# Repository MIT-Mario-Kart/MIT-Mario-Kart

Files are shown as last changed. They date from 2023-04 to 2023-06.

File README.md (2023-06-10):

# MIT - Mario Kart

## Intro
In this project, we planned on creating our own adapted version of Mario Kart in real life. 
The goal was to create a circuit on which we would have 6 small remote-controlled cars, each car controlled either by an AI or by a player. 
We had imagined a few powerups that cars could collect, that would either affect the car collecting it or the other cars. 
There are three main parts to this project: an overhead camera that extracts simple shapes and colours from an image in order to be able to track each car’s position, 
the track and cars themselves, and lastly the main server controlling each individual car.  
You can find our initial project proposal [here](MIT_Team_Proposal.pdf).

## Summary 

- [Cars](#cars)

  - [Electrical Components](#electrical-components)

  - [Connections and circuitry](#connections-and-circuitry)

  - [Color sensor calibration](#color-sensor-calibration)

  - [3D-design](#3d-design)

- [Circuit Design](#circuit-design)

- [Phone Holder](#phone-holder)

  - [MDF structure](#mdf-structure)

  - [3D printed holder](#3d-printed-holder)

- [iOS Application for Cars Detection](#ios-application-for-cars-detection)

  - [Reliable Coordinate System](#reliable-coordinate-system)

  - [Calibrating the circuit](#calibrating-the-circuit)

  - [Detecting cars and their orientation](#detecting-cars-and-their-orientation)

  - [Performance](#performance)

  - [Potential Drawback](#potential-drawback)

- [AI Algorithm](#ai-algorithm)

  - [Overview](#overview)

    - [Flowmap](#flowmap)

    - [Acceleration](#acceleration)

    - [Powerups](#powerups)

    - [Overtake](#overtake)

  - [AI Simulation](#ai-simulation)

- [Server](#server)

  - [Overview](#overview-1)

  - [Camera connection](#camera-connection)

    - [ID system](#id-system)

    - [Updating the cars based on the information from the camera](#updating-the-cars-based-on-the-information-from-the-camera)

    - [Grid system](#grid-system)

  - [Car connection](#car-connection)

    - [Boards connection to the server](#boards-connection-to-the-server)

    - [Remote controllers](#remote-controllers-joysticks)

- [GUI](#gui)

  - [Interface](#interface)

  - [Streaming Server](#streaming-server)

- [Final Takeaway](#final-takeaway)

## Cars

### Electrical Components

One challenge was making the cars small enough so that we can have multiple ones driving on the same circuit while still having a fast and precise drive. For that, we decided to use basic but effective electronic components. The list of the components used for each car is as follows:

>- [ESP8266 board](https://www.conrad.ch/fr/p/carte-de-developpement-sbc-nodemcu-esp8266-1613301.html)
>- [ESP32-CAM board](https://www.conrad.ch/fr/p/joy-it-sbc-esp32-cam-module-camera-1-pc-s-2332111.html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)
>- [L298N motor driver](https://www.conrad.ch/fr/p/joy-it-motormodul-2-u-4-phasen-6-bis-12v-carte-de-developpement-1573541.html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)
>- External antenna [(connector](https://www.digitec.ch/fr/s1/product/delock-cable-dantenne-sma-mhf-4-20cm-pour-linstallation-cable-dantenne-cable-dantenne-13123653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) & [antenna)](https://www.play-zone.ch/en/wlan-wifi-antenne-2-4ghz-mit-knickgelenk-sma-male.html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)
>- [Motor](https://www.conrad.ch/fr/p/joy-it-com-motor01-moto-reducteur-jaune-noir-adapte-pour-ordinateur-monocarte-arduino-banana-pi-cubieboard-raspber-1573543.html)
>- [Servo](https://www.conrad.ch/fr/p/reely-mini-servomoteur-analogique-materiau-entrainement-plastique-systeme-de-connecteur-jr-2148502.html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)
>- [Color sensor](https://www.conrad.ch/de/p/joy-it-sen-color-arduino-erweiterungs-platine-schwarz-passend-fuer-einplatinen-computer-arduino-1-st-1503748.html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)
>- [7.4V Lipo battery](https://www.conrad.ch/fr/p/pack-de-batterie-lipo-7-4-v-1000-mah-conrad-energy-1344143-25-c-softcase-fiche-bec-femelle-1344143.html)

The ESP8266 board was used to connect every other component and to make a connection to the server used to control the cars while the ESP32-CAM board was used to stream the point of view of each car on a dedicated server.

### Connections and circuitry 

The electrical components were connected as follows:

```mermaid
graph LR
A[[Battery]] -- 12V --- B{Driver}
A -- GRD --- B
B -- 5V--- D(Motor)
B -- OUT1 --- D
B -- OUT2 --- D
B -- 5V ---E[ESP8266] 
B -- GND ---E
E --IN1 ---B
E --IN2 --- B
C((Color sensor)) -- OUT --- E
E -- S0 --- C
E -- S1 --- C
E -- S2 --- C
E -- S3 --- C
E -- 3V3 --- C
E -- GND--- C
C -- LED-GND --- C
B -- 5V --- F(Servo)
E -- GND --- F
E -- IN --- F
B -- 5V --- G[ESP32CAM]
E -- GND --- G
H([Antenna]) --- G
```

### Color sensor calibration

The color sensor being sensible to the lightning conditions and its distance to its target, it needed to be calibrated to be as precise as possible. The code of the calibration is available on the repo.

A dedicated server was made at the beginning of testing and showed the performace of the sensor as seen below.

https://github.com/albertfares/MIT/assets/91048303/5f766e19-ce79-4871-9765-ed46f7992c80

### 3D-design
We have designed our cars using the software [Fusion 360](https://www.autodesk.fr/products/fusion-360/overview?term=1-YEAR&tab=subscription). The cars are composed of electronics, 3d printed parts and LEGO pieces. The first step was to import all the components into Fusion 360. For the electronic components, we have downloaded some existing models from the library [Crabcad](https://grabcad.com/library), listed below:

>- [ESP8266 board](https://grabcad.com/library/esp32-dev-kit-v1-1)
>- [ESP32-CAM board](https://grabcad.com/library/esp32-cam-1/details?folder_id=6305310)
>- [L298N motor driver](https://grabcad.com/library/l298n-17)
>- [Motor](https://grabcad.com/library/yellow-dc-motor-1)
>- [Servo](https://grabcad.com/library/sg90-micro-servomotor-1)

The color sensor and the battery are the only component for which we did not found a existing model. So we have precisely measured it and we have model it ourself.

We then imported the LEGO pieces. A good way of doing this is to use [BrinkLink Studio 2.0](https://www.bricklink.com/v3/studio/download.page). It's free, easy-to-use and it gives you access to a 3d model of all LEGO pieces. It also lets you assemble parts to build LEGOs directly within the application, but here we're only interested in the 3d model of the parts. Once we have selected the part we want in brinklink, we can't export it directly to Fusion 360. Here's how to do it:

>- In BrinkLing Studio 2.0, select File > Export As > "Collada" (.dae)
>- Use an online converter to convert your file from .dae to .stl. Here is a link to a converter: [Link](https://imagetostl.com/convert/file/dae/to/stl)
>- Import the file into Fusion 360
>- Rescale your lego part to a factor of exactly 0.04

Once all the parts have been imported. We were able to start designing the car. Design is a long and sometimes complicated process. The right solution doesn't come out on the first try, and sometimes you have to try again and again to get it right. There are a number of factors to take into account. In our case, we wanted the car to turn quickly. Which implies to have a small turning radius. One way of calculating it (approximately) is to measure the wheelbase (Wb), the steer angle (Sa) and the wheel width (Ww). The wheelbase is the distant beetween the front wheels and the rear wheels. The steering angle is the maximum angle at which the wheels can turn. 

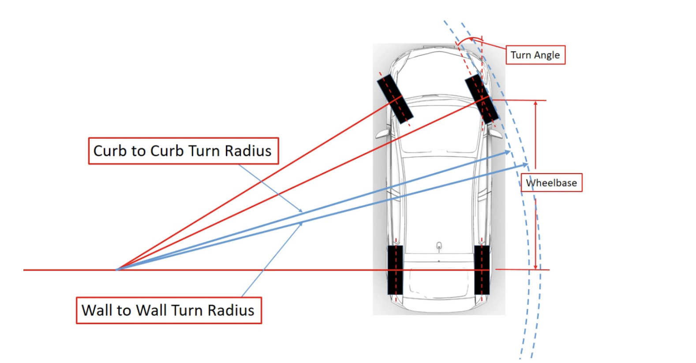
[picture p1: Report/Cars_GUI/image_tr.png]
Image_of_one_Car


[Image source](https://www.theautopian.com/the-engineering-behind-why-some-cars-can-turn-tighter-than-others/)

Once the measurements have been taken, we can calculate our turning radius (Tr) using this formula:   $Tr = \frac{Wb}{\sin(Sa)} + \frac{Ww}{2}$ 

Our car has a turning radius of 165.5 mm.

Here's a link if you want to know more about turning radius: [Link](https://en.wikipedia.org/wiki/Turning_radius)

Another important factor when building a car is the gearbox. Having a gearbox is essential and very useful for a car. When our engine runs, it runs at a certain speed and with a certain torque. In a nutshell Engine torque is the force of your motor's rotational movement. The more torque the engine has, the harder it is to stop. A gearbox is composed of gears, in our case LEGO gears, and is useful to turn the wheels using the motor. With a gearbox, we can do a reduction. A reduction implies that the wheels will rotate at a different speed than the motor. Reducing speed increases torque. And on the opposite, increasing speed reduces torque. If there isn't enough torque, the car won't move. So you need to find the right balance between the two. In our case we wanted the wheel to turn faster than the motor. This can be done by using a large gear on the motor followed by a smaller one. We used this [website](https://evolventdesign.com/pages/gear-ratio-calculator) to calculate the reduction. For our car, we have a 2.0833 gear ratio.

Taking these factors into account, we designed our car. Here's a timelapse of all the design process:

[Video Link](https://drive.google.com/file/d/1rE5q6M1Bsel_EN98zFcnqaiaQ2I-tCT6/view?usp=share_link)

Once the car has been designed, all that's left to do is print out the parts and build the car. 

To print the pieces, we used a Prusa printer (Original Prusa i3 MK3S & MK3S+) with a PETG filament. To use these printers, you need the [PrusaSlicer software](https://www.prusa3d.com/fr/page/prusaslicer_424/). Here are the steps to follow to print a part:

>- Select you part in Fusion 360 and click on "3d printing". Fusion 360 will then export an STL file.
>- Import the STL file into PrusaSlicer.
>- Click on "cut now". It will export a gcode file. 
>- Select the gcode file on your printer.

Of course there are a number of things to be careful about when printing. It's important to get the right settings. In our case, we used the default settings with a quality of 0.15 mm. It is also important to add support if necessary. When you need to print with support, you then have to remove it, which sometimes results in lower-quality parts. So we have designated our pieces to have to put on as little support as possible. We have divided our printing into 2 sets. The first set (Set_1_S) takes 4h42 and 39.18 g of filaments. The second set (Set_2_S) takes 4h13 and 37.89 g of filaments. Therefore a car takes a total of 8h55 and 77.07 g of filaments.

Here is a short animation showing how to assemble the car:

[Video Link](https://drive.google.com/file/d/1SugGETj4QmX7_Ma__iNNMzapm10kMvRc/view?usp=share_link)

Here are some photos:

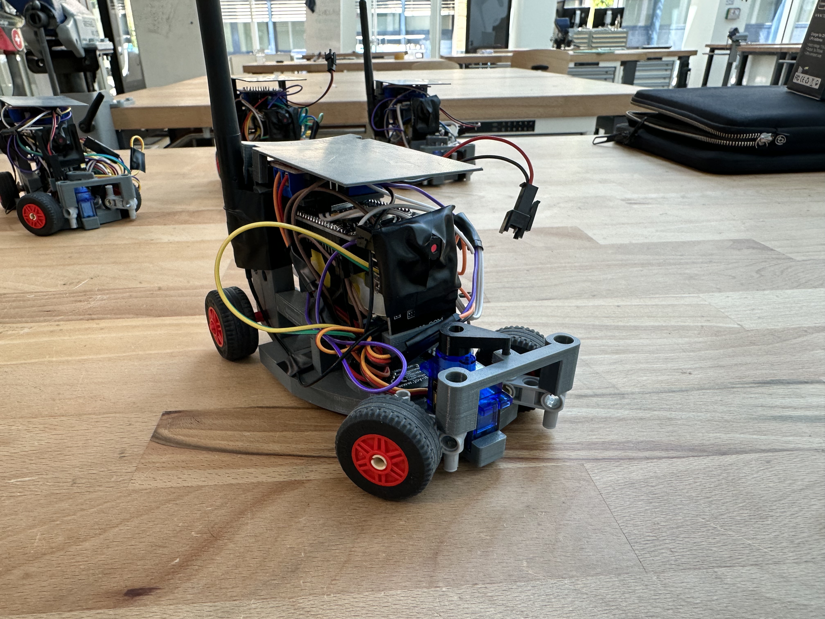
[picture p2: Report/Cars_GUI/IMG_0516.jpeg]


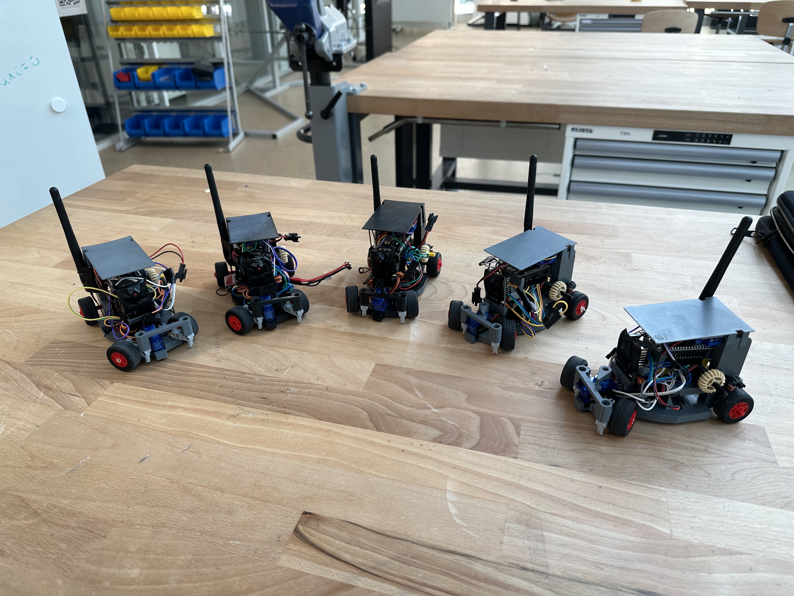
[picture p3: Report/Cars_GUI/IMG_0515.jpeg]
Image_of_the_6_Cars


Here is a video of the car driving:

[Video Link](https://drive.google.com/file/d/1jisL-YeDmEC7GNVOm17FnNlMF6QsF6Wv/view?usp=share_link)

For more details about the 3d model of the car, you can download the file LEGO - car.f3z from the repository.

## Circuit Design

The design of the circuit was made using Fusion360.
The main design of the circuit is shown below.



We then chose to laser cut the circuit on 3mm MDF boards, so we had to make a puzzle like design for both cutting and easier transportation and storage. The full .dxf file is included in the repo.

The laser cutting used aprox. 3 1.6x2m boards.

The final circuit looked like this:



## Phone Holder

### MDF structure

To hold the iPhone used to track the cars 3 meters above the ground, we had to be creative and make a phone holder that was attached to the railing of the DLL's first floor. The structure was laser-cut on 1cm MDF boards and was designed on FUSION 360 (.dxf design file available on the repo).
To make the phone holder strong and reliable, a puzzle-like design was used between pieces and the connections were strenghened by wood glue.



### 3D printed holder

To hold the iPhone in place, a custom designed holder was 3D printed and mounted on the MDF structure. 
The .f3d file available on the repo was made for an iPhone 14 Pro Max.





## iOS Application for Cars Detection

We needed a robust, latency-free car detection and coordinate system to feed the server to complete this project. We decided to go with what we had on hand, and use one of our phones to do the job. So we developed an iOS application in Swift and C++ (because we had to bridge OpenCV in C++, as a Swift version didn't exist).

Our first approach was to use machine learning to recognize the cars, but we quickly abandoned this idea as it was complicated to set up a model that corresponded to our cars, and the results were not very convincing.

So we turned to OpenCV, an open source computer vision library, for this task. As the library offers efficient tools for keeping only a particular range of colors and detecting shapes, it was perfect for our case.

### Reliable Coordinate System

The first challenge was to establish a reliable and precise coordinate system, which initially stymied us because we hadn't taken into account the radial distortion created by the phone's lens. Tangential distortion can occur when a camera lens is not perfectly aligned or when the camera sensor is not parallel to the subject but that's not the case here as the phone was placed to be perfectly parallel to the circuit.

<br>
<p align="center">
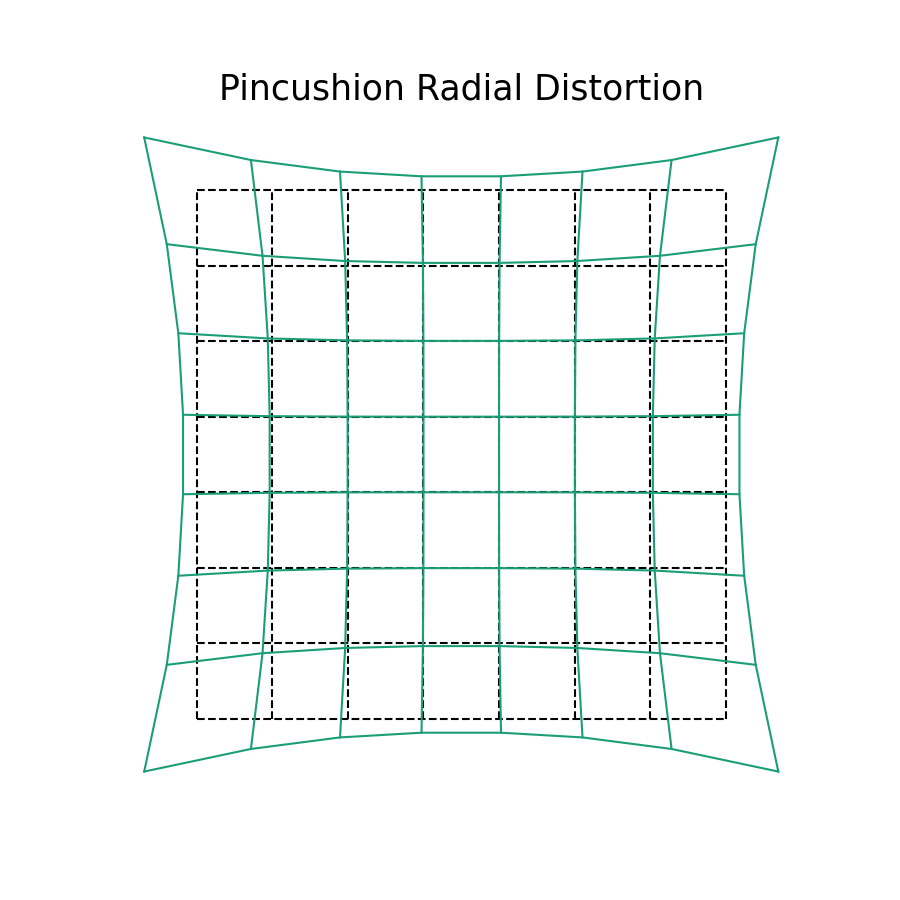
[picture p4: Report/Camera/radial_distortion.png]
Radial Distorsion
  
  <br>
  Illustration of theorical radial lens distorsion
</p>

Fortunately, OpenCV makes it easy to correct this distortion, and the hardest part was calibrating the camera and finding its distortion coefficients. For those curious about this, the [OpenCV Calibration](https://docs.opencv.org/4.x/dc/dbb/tutorial_py_calibration.html) page is very well documented.

<p align="center">
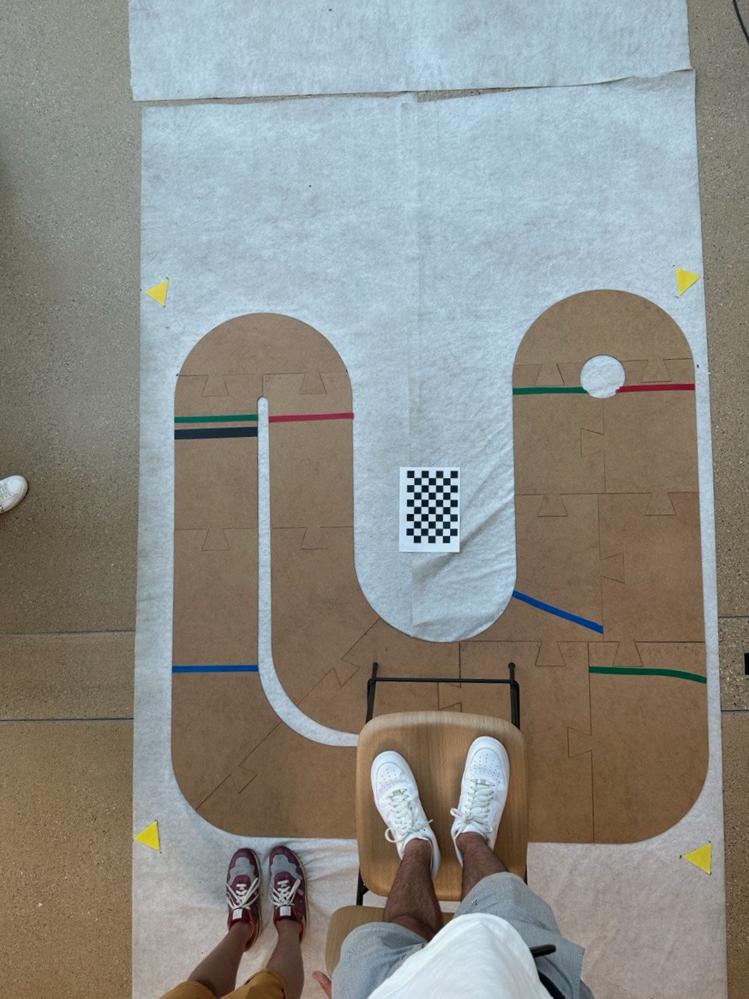
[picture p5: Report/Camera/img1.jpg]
Illustration of lens distorsion
  
  <br>
  Image illustrating the effects of lens distortion at a height of 2.50 m above the circuit where the phone was fixed. The circuit forms a rectangle, but you don't get this impression when you look at the photo because of the distortion. 
</p>

### Calibrating the circuit

Once we had a reliable coordinate system with lens distorsion corrected, the next step was to calibrate our circuit properly. 

When launched, the application launchs in calibration mode. To calibrate the circuit properly, we chose to place a triangle in each corner of the circuit (yellow equal-sided triangle here). The coordinates of these 4 triangles are sent to the server so that it can match the coordinates in the flow map with the coordinates sent by the application.

Here's the technical process for detecting yellow triangles: 
- Request a new image from the iPhone camera.
- Transform it into the OpenCV image format (Mat format) and un-distort it (correct for lens distortion).
- Apply a yellow filter to retain only the yellow elements of the image.
- Perform shape detection on the image and keep only the triangles.
- Obtain the center of each triangle in the iOS coordinate system.
  
If we detect exactly 4 triangles and the positions have been the same for 5 seconds, we send these positions to the server.

Once the server has confirmed that it has received the positions, the application switches to car detection mode. The application also retains the points it used to calibrate, so that any potential false positives outside the rectangle formed by the calibration points are filtered out and not sent to the server.

<p align="center">
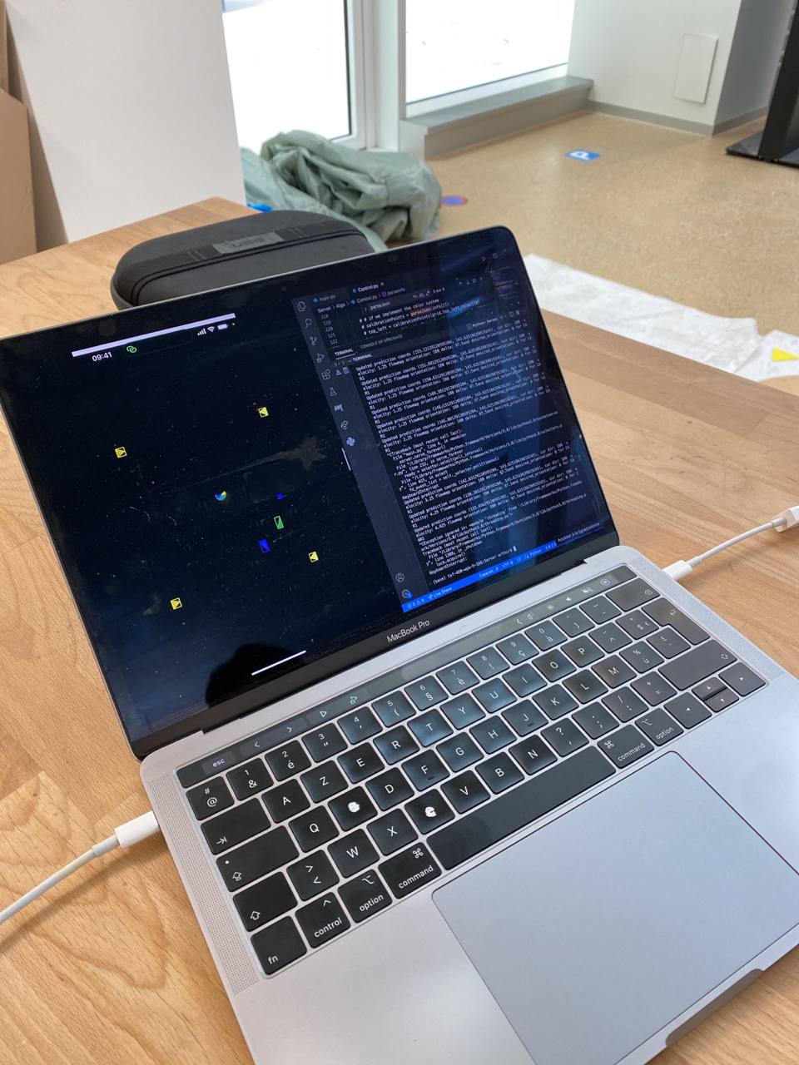
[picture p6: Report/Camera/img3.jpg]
Calibrating the circuit
  
  <br>
  Each of the yellow triangles is placed in one of the corners of the rectangle formed by the circuit. They are used for calibrating the coordinate system.
</p>

### Detecting cars and their orientation

Now that the server is calibrated and we have our coordinate system, we just need to detect the cars and their orientation.

We therefore decided to equip each car with an isosceles triangle of a very distinct color. The isosceles triangle because a triangle is one of the least common shapes in a commonplace environment, and isosceles to detect the orientation of the car. The orientation detection works as follows: we detect the triangle, then its smallest side, we then draw a perpendicular to the center of its smallest side, which allows us to find the car's orientation in degrees using basic math.

Here's the technical process for detecting cars and their orientation:
- Request a new image from the iPhone camera.
- Transform it into the OpenCV image format (Mat format) and un-distort it (correct for lens distortion).
- For each car's color:
  - Apply a color filter to retain only the elements of the car's color in the image.
  - Perform shape detection on the image and keep only the triangles.
  - Obtain the coordinates of the intersection of the two longest sides of the isocele triangle, which we'll use as the car's coordinate. 
  - Identify the smallest side and draw a perpendicular to its center to obtain the orientation of the car (0-360 degrees).
- Send to the server the position of each car and its orientation.

<p align="center">
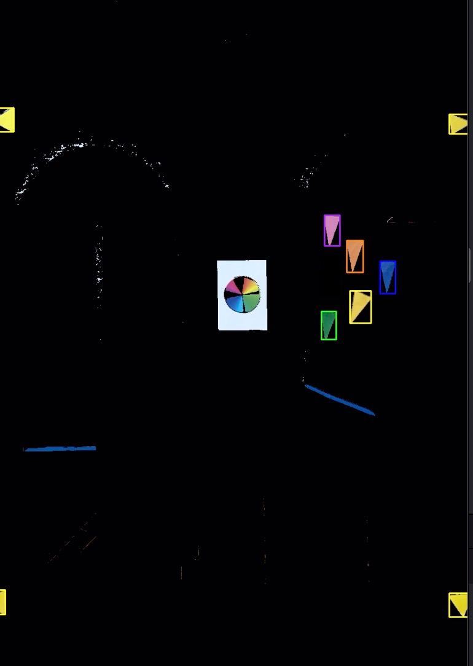
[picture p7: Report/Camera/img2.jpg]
Detecting cars
  
  <br>
  Screenshot of the application in cars detection mode. Each car is detected by the application and indicated on the screen by a rectangle of the corresponding color. The information is sent to the server.
</p>

### Performance

In terms of performance, the application was able to recalculate car positions and orientations and send them to the server 10 to 15 times per second.

### Potential Drawback

One drawback is that to avoid false positives, the color calibration had to be very precise, and is only accurate for a certain time slot (depending on the amount of sunlight entering the building where we calibrated it). As a result, there were occasional false positives on certain colors, particularly in the evening when there was no sun. This can of course be adjusted by recalibrating.

## AI Algorithm
### Overview
The main goal of this project is having cars controlled by players and cars running by themselves (AI controlled cars). In order for the autonomous cars to do a complete lap, they have to follow predetermined directions i.e a flowmap.
#### Flowmap
A flowmap is a map of desired orientation across the circuit, which we separated into a 40x40 grid. For greater clarity in the code, we chose to represent these orientation as hours on a watch (h3 => 0 deg, h12 => 90 deg, h6 => 270 deg, etc...). At each step the car's orientation (the attribute Car.orientation) is compared to its desired one indicated by the flowmap and a change of direction is applied accordingly.

We then calculate the desired steering angle to send to the Arduino which lies between 0 and 180, 90 meaning going straight.



#### Acceleration

Having cars following orientations is great, but in practice the cars take time to turn and their orientation doesn't change immediately. We needed the cars to slow down when approaching sharp bends.

We designed a zone system where each zone has a maximum speed allowed. These zones are bounded with coloured tape on the circuit. There are 3 types of them (ordered in decreasing speed): Green, Blue and Red.

In the Arduino code, the "currZone" variable is either green for full speed, blue for normal speed or red for low speed. Then the variable "speed_percentage", which is determined by the zones, is either 1.25, 1.00 or 0.75.
When a car drives over some tape, its colour sensor detects it and the above-mentioned variables are updated. 
There is also an "out" zone which corresponds to speed_percentage = 0.00 and white colour for the white tarp below the circuit. When a car steps out of the road, it must be placed back on the circuit to continue.

At each step the server sends the variable "rcvd_acc" to the Arduino. We then multiply this value by speed_percentage and give this value to the analogWrite method for the motor. If rcvd_acc is negative we apply it to the PIN_REVERSE instead of the PIN_FORWARD.

#### Powerups

In addition to the red, green and blue tape, we put brown tape on the circuit for powerups. When the sensor detects it, the variable "isPowerupd" is set to 1 and sent to the server. When the server receives it, a random powerup generator is started.

Powerups can have positive or negative effects : 
The first one is to increase your speed by changing Car.acc, the second one is to slow down every other cars and the last one is to invert the commands of all players (not AI) by changing Car.inverted.
The circuit was too narrow so we couldn't implement the last one.

Each powerup lasts 5 seconds as shown below : 
```python
    if self.isOnPowerUp(car):
        if car.startTime == -1:
            pu.powerUp(car, self.cars)

    if car.startTime != -1 and (datetime.datetime.now() - car.startTime).seconds >= POWERUP_TIME:
        car.startTime = -1
        car.acc = pu.NORMAL
        print("STOP POWERUP")
```          

With POWERUP_TIME = 5.

Note: since there were times when testing where the color sensors weren't fully calibrated or times where they produced false positives, we added on the server the same logic described above for powerups and acceleration to use if we wanted to disregard the input from the color sensor. However, in the final version of the project we didn't need to do so but still we left this code commented out (so you could see what how we used it).

#### Overtake

With the powerups and the zone system, cars can have different speed across the map. We didn't want them to bump each other (at least not the AI ones) so we had to implement an overtake system.

At first we thought about delimiting a semi-circle behing each cars. When another car drivees into this area, it starts changing its orientation (car.delta) to overtake. This change is proportional to the distance between the two cars. If they are really close, the overtake needs to be more brutal than if they were far away.

But we had problems with Matplotlib (which we used for the semi circles) and the circuit was too narrow to overtake smoothly. So we implemented an slowdown method which calculates a rectangle behind each car and forces the other cars to slow down (changes car.acc) when they are in it.

### AI Simulation
When it comes to AI Simulation the main component was update movement. This is a method that we used in order to test the flowmap. We made it possible to simulate the way a car would (in theory) follow the flowmap in the GUI. This method wasn't used in the final server, but it proved to be very useful in calibrating a first version of the flowmap. The "orientation" around the flowmap uses the classic trig circle: 0 degrees points to the right of the circuit, 90 degrees to the top, 180 to the left and 270 to the bottom.
The way the method works is very simple - it takes a desired velocity and angle as parameters, and computes the next speed, acceleration and coordinates the car would have and stores them in the car's corresponding attributes. 
At first the car's orientation is updated. If the desired angle is negative, this means that the car should turn right (think of it as a negative angle difference on the trig circle, so clockwise), otherwise it should turn left. If the absolute angle difference between the desired angle and the current angle is smaller than ANGLE_PRECISION (an aribitrarily defined constant, to be tweaked as you see fit), then the car won't turn. Whenever it turns, it does so by ANGLE_UNIT every time the method is called.
Next, the method checks which is the desired velocity and updates the car's acceleration and velocity accordingly using basic kinematic equations, implemented in a very naive way. Technically, the way it's coded you can simulate the car's acceleration changing over time, but we tweaked the constants to give it an almost constant acceleration because we didn't need the added precision (if ACC_UNIT = MAX_ACC, then you will get a constant acceleration). Next, the car's speed gets updated according to its acceleration. Both the acceleration and speed are upper bounded (respectively MAX_ACC and MAX_VELOCITY).
Finally, the car's coordinates get updated according to the car's speed, previous position and current orientation. Keep in mind, this method will never be 100% precise, but it works well enough with the constants calibrated to the right values.

## Server 
### Overview
Everything in this project was connected to our main server. It controlled the AI driven cars and processed the input from the remote controllers and sent it to the player cars. It also took input from the camera to know where the cars were on the circuit which was then displayed on the GUI and used for the AI algorithm displayed above.

We used the ThreadedTCPServer library to open a thread for each new connection and then defined a method that was used to handle all newly received information and send back the information needed by the cars or the camera.

The Control class is used to process the information sent to the server and is responsible for figure out the information to send back to each connection.

### Camera connection 
The server receives from the camera, the position and orientation of each cars. Each car object on the server has a `color` attribute, which corresponds to the color of the triangle on top of the car which is detected by the camera. 
#### ID system
The server recognises that the input is from the camera because the camera precedes all its messages by an id "CAM". The same technique is used by the cars to identify themselves: each car has a specific id. This makes it so that the only IP address necessary to know is the server's (the camera and cars need to know where to connect to). The server will then reply to connections from the camera and cars but we don't need to input their IP in the server before hand.
#### Updating the cars based on the information from the camera
The server then stores the coordinates of each car and its orientation and calls `moveCar` which will look at the flowmap to find the desired orientation of the car, calculate the delta sent to the car (angle that needs to be applied by the servo) based on that information and will figure out the acceleration that needs to be sent to the car based on the zone it currently is in (if we are not using the color sensor).
#### Grid system
Since the coordinates sent by the camera are originally within 1080x1920, we need to translate to the actual coordinates in real life. To do so, we use the coordinates of the 4 yellow triangles sent by the camera when it is in calibration mode and use this info to establish a grid. Then, for all future coordinates sent by the camera, we use this grid to translate them to real life positions. Once the server is calibrated, it connects back to the camera to tell it to exit calibration mode.

### Car Connection
Each car connects to the server with a car id. The server uses this id to get its corresponding car object on the server and sends back to the car, the correct information. Either the orientation and acceleration found using the algorithm if it's an AI driven car or the information processed using the controllers for player cars.
#### Boards connection to the server
The ESP8266 boards each connect to the main server over wifi, which must all be connected to the same wifi. For this we used the personal hotspot of the phone acting as the camera, which proved a little unreliable as it sometimes decided to become undiscoverable on its own. We often had to resort to yelling "hey Siri, open hotspot settings" while standing on a chair in order to be closer to the phone. 
Once the boards were connected to wifi, we had them connect to the server using WifiClient from the ESP8266WiFi.h library. The boards would send colour sensor information in the form of an integer between 0 and 5, indicating what kind of checkpoint the car has passed (while it isn't passing a checkpoint, it perpetually sends a 0):
0 = circuit, 1 = powerup, 2 = red tape, 3 = green tape, 4 = blue tape, 5 = car is off the circuit
The boards then received all movement data straight from the server, in the form of 2 integers. The first received integer indicated the value to be weitten to the car's servo (between 0 and 180, inclusive). The second indicated the car's speed: a negative integer meant that the car should drive backwards, a positive integer meant that the car should drive forwards and 0 meant stop. 
To separate these two integers from the received string, we used strtok() to separate the string and atoi() to convert the numbers in the string to the int type.
Two important elements we overlooked that probably greatly contributed to server-board latency were the heat produced by the motor on the car (which probably greatly slowed the board down) and the interference caused by other electronic devices in the near vicinity. There were never that many people around us before the demo day, but when people started arriving the day of the demo, the cars connected to the personal hotspot but never to the server.

#### Remote controllers (joysticks)
We faced more challenges than we had anticipated for the joysticks controlling the car. First, we tried using Blynk, except that we couldn't get the Arduino to connect to Blynk's servers and to our server both at once, and we still don't know why. 
Next, we tried reusing and adapting the code one of us had written to control the cars we each made for the personal project (different cars to this project). It worked by hosting a webserver directly on the Arduino using the ESP8266WebServer.h library and then connecting to that webserver using a phone (with the Arduino connected to that phone's personal hotspot). The joystick worked perfectly while not connected to the server, but had terrible latency issues when connected to the server at the same time as hosting the webserver.
In an attempt to fix this, we tried using the car's second board (the ESP32-Cam-AI-Thinker). The idea was to have the ESP8266 host the webserver and have the ESP32 communicate with the main server, and then transmit any data received from the main server over the two boards' Serial ports, using the RX/TX pins and the SoftwareSerial.h library. Unfortunately, we again ran into high latency issues. Anyone who wants to use the SoftwareSerial.h library should know that it takes a lot of processing power and therefore slows the board down. In theory, it's possible to communicate over Serial without using this library, but by this point we were running out of time. Serial communication is painful and long to debug, because you can't send messages to another board over Serial and print received messages to the console at the same time, so you need to be a little creative (to test it out, we connected both boards to a dummy server that just prints messages and had each board transmit any received from the other board). Therefore, we were forced to downgrade to a system where powerups could only affect one car at a time until we came up with our final solution: console controllers connecting to the computer hosting the main server, and the main server sending on the movement data the the ESP8266.

This final solution was implemented using pygame because it already had a way of detecting a controller once it has been connected to the computer using bluetooth (Note that this module supports xbox one and 
pro Switch controllers perfectly, but for reasons unknown we were unable to get ps4 controllers to work). So what we ended up assigning to our car object a controller from the Controller class if a JOYDEVICEADDED event from pygame was added and if the car was a player driven car. Then we updated each car object constantly by looking at the joystick position to figure out the angle to send to the car and if the forward or backwards button were pressed, to figure out what acceleration to send the car. As described above, the same arduino code was used for player and AI cars so we send that information to the cars in the same way as we did for the AI car. This lets us decide for a given round what cars will be AI or player driven without reuploading arduino code, this is done by simply changing the `ai` attribute of the car when initialising the car object.

[Video controller_1](https://drive.google.com/file/d/1reOZbyJa6JoQu1c-rn_mInbwud_DtXWd/view?usp=sharing)

[Video controller_2](https://drive.google.com/file/d/1dASTlvPD5uQj2d0VwFhFrCf5u4_w9qwt/view?usp=sharing)

## GUI

To make our project more complete, but also more fun to play, we decided to add a GUI (Graphical User Interface). Since
our server was already coded in python, using pygame seemed to be the best solution. 
### Interface
The interface is fairly simplistic. 

Image_of_the_GUI

On the left, there is a map of the circuit. On this map, a colored square indicates the position of each car, and a color 
is associated with each car. Above the circuit is the start light. It is red at the first, and turns green when the race begins.

On the right, there's a classification. In the upper right-hand corner is a timer. The timer starts when the race begins. 
Below this is the ranking for each player. The number on the left corresponds to the player's position. Then the player's name. 
To the right of this is the player's lap time. This is a measure of the time it takes the player to complete a turn. This 
time resets to 0 each time the starting line is crossed, provided all checkpoints have been passed.  Then there's the player's 
best lap time. On the right is a lap counter. This shows the player the number of laps remaining. A lap is added each time 
the player crosses the start line and has passed all checkpoints. Next, the power-up is displayed. Each time the player has
a power-up, it is diplayed here with an image associated with each power-up. Finally, when the player has finished the race. 
That is, when he has completed the correct number of laps, a small flag is displayed, showing that the player has finished.

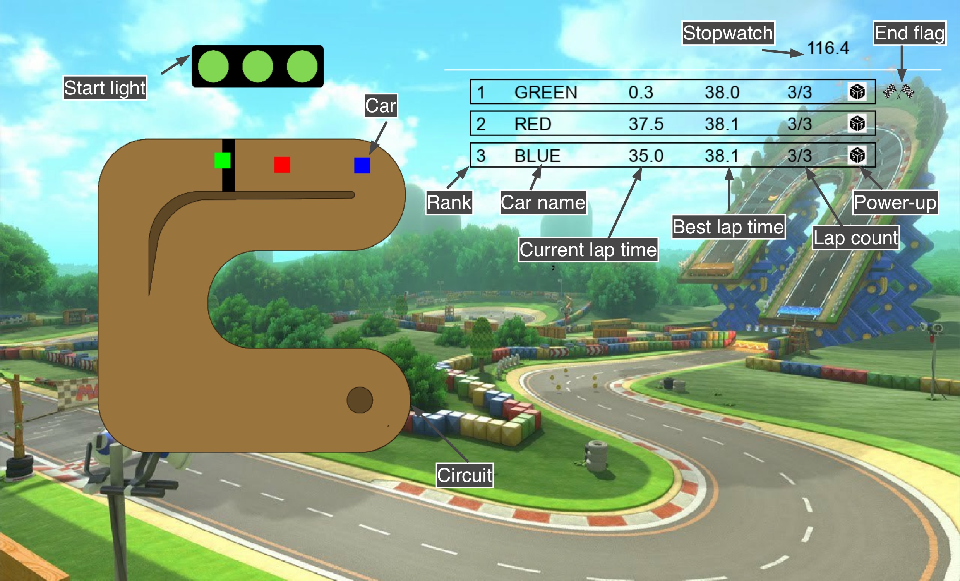
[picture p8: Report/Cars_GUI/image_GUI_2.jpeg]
Image_of_one_the_GUI_with_legends


Here is a video showing the GUI with a game (without power_up):

[Video Link](https://drive.google.com/file/d/1Wopnna9PGnGgz63frg08rsFXboGv2CES/view?usp=sharing)

### Streaming server

To stream each car's pov, we used an esp32 cam on each car which streams continually on a custom server. The code used to enable the streaming on the boards allows to chose the quality and format of the video output. We personally went with the SVGA format and a quality of 63 (to have a fluid stream). All the videos are then combined on a streaming server which can handle up to 6 cars' povs. The code for the server and the html design are both on the repo.

It looked like this:



## Final Takeaway

The final project state was a working racing game with 3/4 of the previously planned cars even though the AI lacked a little in precision.
Unfortunately, there was one important element we had not anticipated: wireless interference. The day of the demonstration, 
we were unable to demonstrate that our project was in fact functional, because the Arduino boards used in the cars refused to connect to the main server. This is due to increased interference when everyone starting demonstrating their project around us at the same time.
Nevertheless, you will find a video attached showing the project in a functional state, using AI cars.

[Video Link](https://drive.google.com/file/d/1U7BNgFku9bf5cgFWT6QTgowsCUX8AMdn/view?usp=share_link)

The problem that slowed us down the most was certainly latency in general, because it was at first very hard to pinpoint the problem, then it took a while to try to resolve it (the problem has no known solutions so far, other groups had the same problem and were unable to solve it).

We also underestimated the time necessary to put all of the different components of the project together. They all worked
fine alone, but once we put them together a lot of new bugs started popping up, probably because we did so only at an advanced stage of the project.

At the end of the day, it was a complex project and we learned a lot from hardware to software and the link between the two, with TCP connections, computer vision, 3D printing, handling wood and other materials. Don't hesitate to reach out to us if you have any questions.

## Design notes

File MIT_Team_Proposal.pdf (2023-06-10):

# CS-358 MIT: Team Proposal

Arthur Bigot Rokhaya Fall Albert Fares Hugo Jeannin Thomas Kemper Daniel Polka

April 2nd 2023

## 1 Description

The main idea of our project is to recreate a real life version of the worldwide famous video game MarioKart. We would have 3 cars and potentially 3 controllers that would be designed by us and then 3d printed. There will be two ways to play the game, the first is challenging autonomous cars controlled by AI and the second playing against real players. Numerous power ups will be available for the players to pick up on the track to make the experience more fun.

### 1.1 Hardware Description

### 1.1.1 Cars

For the cars, we’re looking for a minimalist and relatively small design, which also packs power and precision. The car design will be specially designed and 3d printed to hold all the electrical components and have an aerodynamic silhouette. It will be a 4 wheel car, rear wheel drive. The aimed dimensions are max 20x10cm. For better precision in turns, we will implement a differential steering. The two front wheels will be steered using a servo. A color sensor mounted to the bottom of the car will track colored tape scattered on the circuit. The color sensor will be used to check that the car makes a full lap, but also to give “power up” to the car. In MarioKart, there are items that can be collected as power ups. In our project, a certain color will correspond to a power up. We can imagine different power ups: the car goes faster, the other car goes slower, it stops the other car,... We have chosen the following components:

Motor: We decided to use the same engine as for the LEGO car. It is powerful enough for the size of our car and already has an integrated gearbox. Moreover to increase the speed of the car, we think to print in 3d gears to change the reduction ratio and to have in our case a less strong reduction.

Servo: We will use the same type of servo we used on our individual projects.

1

Board: We will use the ESP32 with camera so we can stream what the car sees.

Motor driver: We decided to go with the L298N driver to control our motor. It is well adapted to the motor we have chosen.

Battery: We will use a 1000mAh 7.4V lipo battery to provide a fast and long lasting experience.

Battery protection: We will use a XL6009 Buck-Boost Converter. The input voltage is 5V - 32V which is well suited to our 7.4V battery. Moreover the output voltage is adjustable and allows to have 1.25V - 35V which is perfect for our motor controller which receives 5V maximum.

Battery charger: To charge our the lipo batteries we are using, we will use a lipo battery charger.

Differential: We will use the LEGO differential (number 6573). It corresponds well to the size of our car and very robust enough. This differential works with 3 gears. (number 6589)

Wheel: We will use LEGO wheel. We have chosen the wheel number 56145 and the tyre number 55978. Those rim and tyre are bit larger (22 mm against 14mm) than the ones we used in the first project. We find them a bit more racing and more suitable for MarioKart cars.

### 1.1.2 Tracks

For the circuit, we’re going to keep it as cheap and simple as possible: we want a big enough track to make it interesting, and for this we would like to use a total of 4m²
in fiber blocks (divided into 16 50cm x 50cm blocks). We would like to store these blocks in the DLL storage room (by stacking each 50cm x 50cm block on top of each other to save space, the blocks won’t be permanently stuck together). To assemble the circuit, we would then only have to put these blocks next to each other on the ground.
The circuit borders will be delimited by black tape, and if we have the time at the end of the project we will design and print 3D walls as well. The “power up lines” and “checkpoint lines” will be marked by colourful tape.
Since we don’t know how far away the camera can be from the track for the tracking to work properly, we have designed two different tracks. The cars will end up measuring about 9cm in width, so the width of both tracks varies between 20cm and 30cm so that overtakes will be easily doable (track areas with a width of 20cm are not intended as overtaking areas). We have a diagram for each track, where each square represents 10cm in real life. The first circuit is 2m x 2m (see figure 1) and the second is 1.5m x 1.5m (see figure 2). The

2

general circuit outline is in black, the bridge is in blue, the fiber blocks are represented in green and a 5cm border is represented in red (we think that there should be at least 5cm in between the edge of the track and the edge of the fiber block surface). This is a detail, but even if there is a bridge on the circuit (to make it more interesting), it won’t cross another part of the track, because the only way we will have to track the cars will be using the camera above the circuit, and without other sensors, a bridge crossing over the track would cause a problematic blind spot in the tracking of the cars.
The phases to build the track are very simple, for this reason the only deadline we are fixing is to get the track done as soon as we receive the fiber blocks and tape. We will start as soon as we get the fiber blocks and aim to finish it straight away since it will be done quickly and will be indispensable for testing:
- Assemble the fiber blocks
- Mark the track borders with tape (and cut the tape at points where it crosses two blocks)
- Mark the track power ups and the track checkpoints

We will use a tripod to hold the iPhone flat at 3.3m above the circuit. We need it to be as stable as possible for optimal precision, and it always has to remain at the same position relative to the track.

3

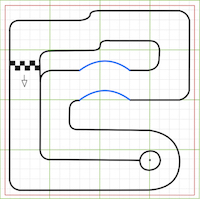
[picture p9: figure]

Figure 1: Big circuit

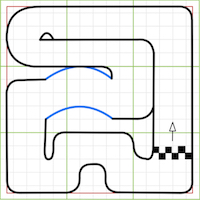
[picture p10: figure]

Figure 2: Small circuit

4

### 1.2 Software description

In this project, cars will either be remotely controlled or be driven by AI. Remote control will be done via remote controllers. The main hurdle software wise will be to implement the latter. To do so, we would implement a centralized main server that coordinates the actions of the AI driven cars.

The main server would receive two main forms of input: coordinates of the cars and distance between each cars coming from an iOS Application using the device camera, standing above the circuit and color sensors data from on-board sensors of the cars.

### 1.2.1 iOS Application - Vision Computing and ML

The iOS Application using the device camera would serve to establish a coordinate system and measure distance between the cars. It will use the Vision Framework (https://developer.apple.com/documentation/vision) by Apple combined with the Core ML Framework (https://developer.apple.com/documentation/coreml) that will allow us to use Machine Learning in our application to detect the cars using a trained classification model on 3 different images, each clearly different (one image per car, each placed on the roof). The application will be written in Swift. Depending on time limitations, we will either take some already trained models for the three different images or compose the database and train the model by ourselves (taking pictures, labelling them, etc..).
The coordinate system established by the application will be based on the position of the phone with respect to the circuit. Therefore we will always place it at the same position with respect to the circuit using a custom tripod made out of wood.
The coordinates of each car and the distance between each cars will be sent to the server multiple times by second. Processing it on the server side will allow us to determine the real orientation and speed of each car. (The server already having the theoretical orientation and the theoretical speed because it controls the cars and will be able to adjust those values thanks to the real values computed).
For the communication between the iOS and the server controlling the cars, we were thinking of using the UDP for the transmission protocol. Indeed, we don’t care about lost packets here and therefore re-transmissions as data will be sent multiple times per seconds. To be sure we don’t face packets reordering, we will add a sequence number to each packet we send so that the server know in which order the packets were sent and can process them accordingly.
We already have a first draft of an application detecting QR codes on an iPhone using the frameworks mentioned above (we used a trained database (https://universe.roboflow.com/lihang-xu/qr-code-oerhe) of QR codes) that is very effective, it doesn’t compute coordinates or distance between them yet.
Even if we are quite sure that we are going to get the application working considering the code we already have working; if it does not work, we will use

5

a webcam for the overhead camera and use the code from ”Intelligent Traffic Backend” but this will have more latency (and the webcam will need to be taken into account in the budget).

### 1.2.2 iOS Application

Since the controllers are too expensive to make, we will also make an iOS application (a different one) that enables a player to control a car from their phone. Controlling one of the cars will be the application’s only point.

### 1.2.3 Individual Car Servers

Each car will have a local server receiving inputs from the main server and sending the data from its color sensors to the main server.

In terms of communication between the main server and the cars servers, the idea would be to open a UDP socket between the main server and each of the cars. We would rather use UDP than TCP because dropped packets are not too much of an issue here as the goal is to have the lowest latency possible. We will include a sequence number in each packet header and process the packets accordingly on the main server and car server side to avoid packets re-ordering. Each car will then be set up with the IP and Port of the UDP server socket.

The overall goal of the server we want to set up is to process the data received as fast as possible and send back inputs to the cars ideally more than 10 times per second. The code on both server and car sides should be very lightweight and optimized to allow fast processing and transmissions.

The color sensors will serve to detect checkpoints and power-up stations (as explained before in section 1.1). If it’s a power up, the car will directly process it and activate the effect, we don’t need a round trip through the main server that would add latency. The information that the car has crossed a power up or a checkpoint will still be sent to the main server so that the information is displayed on the GUI.

### 1.2.4 Main Server - Model Predictive Control (MPC)

The cars will be controlled from the main server using Model Predictive Control with the IPopt solver. (https://coin-or.github.io/Ipopt/) This will let us calculate the best set of actions that the car will take at each given step and then pick the best controls to send to each car for the next immediate time step.

The MPC will run on the main server, the main server receiving data from the iOS Application and each car’s server. The main server and the MPC will both be coded in python, in order for us to access optimisation libraries already

6

existing in python. This main server will receive the coordinates in a buffer that will contain the last X samples with each sample containing the (x, y) positions of the cars from the iOS Application as described in the iOS Application section. X will need to be determined through testing but for now, we are thinking of using the last 10 samples. We will then use those coordinates to determine the orientation of the cars and their velocity. These are the values used later on by the MPC determine the correct course of action.

The MPC solver will also need to possess a reference trajectory for the circuit containing the reference position (x, y). This reference trajectory will be hard-coded and the coordinates are within the grid defined by the iOS app. We need to determine if we want to fit a 3rd degree polynomial curve to determine the cross track error cte at each step or if we want to pre-process the waypoints.

The MPC will plan ahead for a certain time-step length N, this will be determined later on because too large of an N will induce a lot of computations that the solver will not be able to provide in real-time (causing latency induced accuraccies) and any model inaccuracies will be compounded for longer periods of times. However if the N used is too small, the model won’t be able to find the best control actions and we won’t have an optimal control policy. We will need to test out different values of N to find the best one.

The MPC will need to receive an input vector containing the state of each car. This is characterised by its position (x, y) in the track (determined by the camera system as explained in the previous section), its orientation angle ψ and its velocity v. The MPC will then give out as output a vector (the actuation signal) containing the throttle a in range [-1, 1] (full brake and full throttle) and the steering angle δ (its range is yet to be determined because this depends on our car model itself). Here is the definition of our vectors in python:

from collections import namedtuple

State = namedtuple (’State ’, [’x’, ’y’, ’psi ’, ’v’]) Actuation_Signal = namedtuple (’ Actuation_Signal ’, [’a’, ’delta ’])

Note: psi corresponds to the orientation of the car and delta to the steering angle.

At each given point in time, we will want to update our state. To do so, we will use the following formulas:

dx = cur .x + cur .v * math . cos( cur . psi ) * dt
dy = cur .y + cur .v * math . sin( cur . psi ) * dt dv = cur .v + act .a * dt
dpsi = cur . psi + ( cur .v/Lf ) * act . delta * dt

Here, dt is our time interval and will be determined through testing. cur is the current state vector and is of type State (definition above). The constant Lf corresponds to the radius of the circle formed by the car with constant steering

7

angle and velocity on a flat terrain and is also yet to be determined as we need the cars to do so.
The formulas are basic kinematic equations of motion that will let the solver take into account the cars’ dynamics.

The MPC solver will need to use a cost function that the solver will try to minimise. The cost function will almost definitely change when we test out the MPC model on the car. Right now, we are taking inspiration for the cost function from ”Model Predictive Control (MPC) for Autonomous Vehicles”. But we will need to fine tune it so that it can really respond to our needs. So for now, we have the following representation:

Weight = namedtuple (’Weight ’, [’w_cte ’, ’w_epsi ’, ’w_roc_a ’, ’ w_roc_delta ’])
Cost_Info = namedtuple (’Cost_Info ’, [’cte ’, ’epsi ’, ’ s_dif_velocity ’])

def cost_function ( act : Actuation_Signal , cost_info : Cost_Info ): cost = weights . w_cte * cost_info . cte
cost += weights . w_epsi * cost_info . epsi
cost += cost_info . s_dif_velocity
cost += math . pow ( act .a , 2)
cost += math . pow ( act . delta , 2)
cost += weights . w_roc_a * roc_a
cost += weights . w_roc_delta * roc_delta
return cost

roc a and roc delta are constants representing the rate of change of the throttle and steering angle respectively, they are yet to be determined since they also depend on the car model. The Cost Info type contains information needed for the cost function:

- the cte attribute represents the squared difference between the position of the current state and the reference position.
- the epsi attribute represents the squared difference between the orientation of the current state and the reference orientation.
- the s dif velocity attribute represents the squared difference between the velocity of the current state and the reference velocity.

These are then determined in the following way:

cte = math . pow ( cur .x- ref .x , 2) + math . pow ( cur .y- ref .y , 2) epsi = math . pow ( math . abs ( cur . psi - ref . psi ) , 2)
s_dif_velocity = math . pow ( cur .v - ref .v , 2)

Each of these attributes including roc a and roc delta have weights attached to them. These weights will help with accuracy control (for cte and epsi) and to guarantee a smooth trajectory (for roc a and roc delta). weights is of type W eight and contains all these weights. The weights will be determined and

8

adjusted through testing.

Since we are running a multiplayer game, we cannot simply directly apply the MPC to each car because they will interfere with one another. In order to fix this issue, we want to take inspiration from the ”Autonomous Racing with Multiple Vehicles using a Parallelized Optimization with Safety Guarantee using Control Barrier Functions” article and use the MPC when there are no other cars around but when there are surrounding cars blocking the path, we will utilise an optimization-based planner which through the use of Bezier curves will let our car overtake others and get back on the track. Here is a representation of this system from the paper itself:

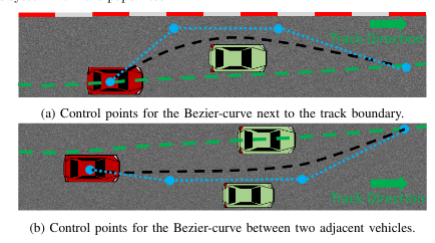
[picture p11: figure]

### 1.2.5 GUI

As a last bonus, we want to implement a graphical interface with a minimap of the cars around the circuit that also displays the speed and direction of the cars, along with the predicted trajectory of the cars based on the AI prediction.

## 2 Related projects

- Intelligent Traffic Backend project (MIT project from last year) (https://github.com/AnirudhhRamesh/Intelligent-Traffic-Backend)
- Example Of iOS LiDAR (https://github.com/TokyoYoshida/ExampleOfiOSLiDAR)
- Wizards-Chess (MIT project from last year) (https://github.com/Wizard-s-Chess/Wizards-Chess)
- Camera streaming library via RTMP, HLS for iOS (https://github.com/shogo4405/HaishinKit.swift)
- Car model (https://www.thingiverse.com/thing:1193309/makes)
- Car model (https://walabot.hackster.io/jonmendenhall/walabot-and-mobile-app-controlled-3d-printed-cars-8d376a)

9

- Model Predictive Control (MPC) for Autonomous Vehicles (https://amitp-ai.medium.com/model-predictive-control-mpc-for-autonomous-vehicles-e0fdf75a9661)
- Autonomous Racing with Multiple Vehicles using a Parallelized Optimization with Safety Guarantee using Control Barrier Functions (https://arxiv.org/abs/2112.06435)
- Nonlinear MPC for autonomous racing example (https://github.com/nirajbasnet/Nonlinear_MPCC_for_autonomous_racing/blob/master/nonlinear_mpc_casadi/scripts/Nonlinear_MPC.py)

## 3 Challenges and risks

One of the challenges we will be facing is attaining the wanted performances for the car especially having a fast enough car and a precise steering mechanism.
- The servo can be tough to calibrate to be exactly at 90 degrees so the car might not go straight.
- The motor gear box we want to buy is too slow so we will need to modify the gear ratio to up its speed. This can be a little tricky because the gears are relatively small and the 3D printing machine is not too accurate for such designs.
- The battery we are using is a lipo battery which can be a little dangerous is not used correctly so we will need to be careful with it and we will use a Protection Module.
- Fiber block could tear if one of us isn’t careful (or if it gets damaged in storage). At least it wouldn’t be a hard fix, but the team would then have to reimburse the damaged fiber block(s) out of pocket. There is also a risk that the cars’ wheels slide on the fiber blocks or that the color sensors don’t detect the tape.

Another challenge, we will be facing is related to the MPC and the optimisation-based planner. Seeing as how we will need to control three cars with these systems, it could become very computationally heavy. If that is the case, we will need to reduce the time step length of the MPC and/or simplify the overtaking system in order to lessen the computations made and simplify the problem of riding the cars.

When it comes to the optimisation-based planner, this may be too hard to develop with the information given to us by the camera. If that is the case, we could scale back the project by preparing different routes for each car in advance and then simly run the MPC on each car without the overtaking maneuver.

For the iOS Application, even if we are quite sure that we are going to get the application working considering the code we already have working; if for some reasons we can not get one of the part working (distance algorithm or coordinate system) or the cars are moving too fast to be recognized or any latency issue, we will use a webcam for the overhead camera and use the code from ”Intelligent Traffic Backend” as a backup solution but this will have more latency (and the webcam will need to be taken into account in the budget).

10

## 4 Components to buy

- 3x ESP32 cam boards (11.95 CHF/piece) (https://www.conrad.ch/fr/p/joy-it-sbc-esp32-cam-module-camera-1-pc-s-2332111.html)
- 3x Motor (5.35 CHF/piece) (https://www.conrad.ch/fr/p/joy-it-com-motor01-moto-reducteur-jaune-noir-adapte-pour-ordinateur-monocarte-arduino-banana-pi-cubieboard-raspber-1573543.html)
- 3x Driver (6.3 CHF/piece) (https://www.conrad.ch/fr/p/joy-it-motormodul-2-u-4-phasen-6-bis-12v-carte-de-developpement-1573541.html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)
- 3x Servo (6.55 CHF/piece) (https://www.conrad.ch/fr/p/reely-mini-servomoteur-analogique-materiau-entrainement-plastique-systeme-de-connecteur-jr-2148502.html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)
- 3x Battery (10.95 CHF/piece) (https://www.conrad.ch/fr/p/pack-de-batterie-lipo-7-4-v-1000-mah-conrad-energy-1344143-25-c-softcase-fiche-bec-femelle-1344143.html)
- 3x Boosters (4.50 CHF/piece) (https://www.elektronik-kaufen.ch/products/xl6009-invers?variant=41643624169648&currency=CHF)
- 3x Color Sensors (9.80 CHF/piece) (https://www.conrad.ch/de/p/joy-it-sen-color-arduino-erweiterungs-platine-schwarz-passend-fuer-einplatinen-computer-arduino-1-st-1503748.html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)
- 12x Tyres (1.57 CHF/piece (ID:4499234/55978) (https://www.lego.com/fr-ch/pick-and-build/pick-a-brick)
- 12x Rims (0.48 CHF/piece (ID:4299389/56145) (https://www.lego.com/fr-ch/pick-and-build/pick-a-brick)
- 3x LEGO differential (1 CHF/piece (ID:4299389/56145) (https://www.lego.com/fr-ch/pick-and-build/pick-a-brick)
- 9x LEGO gear (0.1 CHF/piece (ID:4299389/56145) (https://www.lego.com/fr-ch/pick-and-build/pick-a-brick)
- 3x LEGO gear (0.36 CHF/piece (ID: 6346517/18575) (https://www.lego.com/fr-ch/pick-and-build/pick-a-brick)
- 6x LEGO CONNECTOR PEG (0.05 CHF/piece (ID: 4666579/6562) (https://www.lego.com/fr-ch/pick-and-build/pick-a-brick)
- 6x LEGO axle (0.09 CHF/piece (ID: 370526/3705) (https://www.lego.com/fr-ch/pick-and-build/pick-a-brick)
- 12x LEGO axle (0.09 CHF/piece (ID: 6129995/3705 ) (https://www.lego.com/fr-ch/pick-and-build/pick-a-brick)
- 6x LEGO BUSH FOR AXLE (0.04 CHF/piece (ID: 6271820/42798 ) (https://www.lego.com/fr-ch/pick-and-build/pick-a-brick)
- 16x 0.250 m² Fiber boards (3.13 CHF/piece) (https://www.jumbo.ch/fr/construction-renovation/bois/panneaux-de-bois--decoupe-du-bois/panneaux-de-fibres-de-bois/panneaux-de-fibres-dures/panneau-de-fibres-d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)
- 1x Coloured tape (9.70 + minimum order surcharge of 5.90 = 15.60) (https://www.galaxus.ch/en/s4/product/max-hauri-insulating-tape-15-mm-10-m-10-piece-adhesive-tape-14325303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)
- 1x Tripod (43 CHF/piece + 15 CHF shipping = 56 CHF) (https://www.thomannmusic.ch/millenium_lichtstativ_lst310.htm)

TOTAL = 333.84 CHF (we will pay the extra personally)

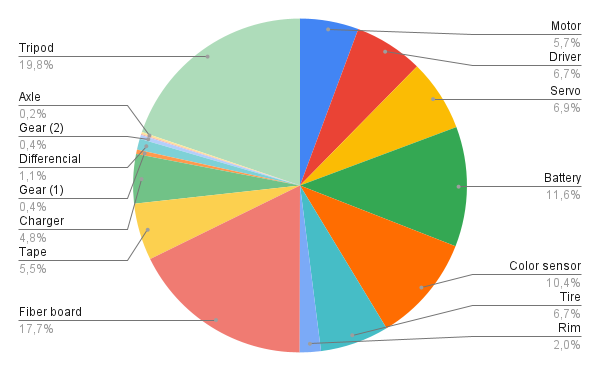
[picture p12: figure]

11

## 5 Structure

In terms of the global milestone, we are setting a goal to have all cars done by week 11 and also have the MPC developed such that if there is only one car on the track, this car will be able to drive and direct itself on the circuit. The car will be able to be detected by the camera using a QR code figuring on top of the car.

We also have more specific deadlines for each aspect of the project separated on a week per week basis per person. These are in the following sections.

### 5.1 Software deadlines

### 5.1.1 Main Server - MPC

- Week 7:
- Rokhaya: Structure the optimization-based planner and define the initial formulas used
- Hugo and Daniel: Figure out the reference trajectory and how to integrate it with the MPC, prepare interaction between the server and the cars
- Week 8:
- Rokhaya: Implement the optimization-based planner
- Hugo and Daniel: Implement the solver into the MPC, prepare integration for the MPC and optimization-based planner
- Week 9:
- Rokhaya and Hugo and Daniel: Begin testing the system on at first one car, start testing out different settings and value combinations
- Week 10:
- Rokhaya and Hugo: Fix errors and bugs discovered in week 9, fine tune the settings, further testing, begin testing with multiple cars
- Week 11:
- Rokhaya and Hugo: Continue testing with multiple cars, adjust the settings, fix errors and bugs discovered
- Week 12:
- Rokhaya and Hugo: Integrate the MPC and the optimisation-based planner with the server
- Week 13:
- Rokhaya and Hugo: Fix the bugs and errors discovered in Week 12, some more fine tuning of the settings
- Week 14:
- Rokhaya and Hugo: Same as Week 13 and finish the documentation of the MPC and the optimisation-based planner

12

Alongside this, each week we will write documentation for the tasks we are working.

Note: there often figures the names of two individuals for the tasks. This is because the work will be done in parallel between the two of us and there is a lot of testing to be done in order to improve our model. So there will be a lot of iterations needed, where a number of different settings and functions will need to be tested out.

### 5.1.2 iOS Application - Computer Vision and Machine Learning

- Week 7:
- Arthur: Set up the application prototype with image recognition for three different type of images (pre-trained model from Robotflow), create the GitHub repository and document the code
- Week 8:
- Arthur: Implement a coordinate system, test the accuracy of the system, check performance wise how many times a second can compute the coordinates
- Week 9:
- Arthur: Implement the distance algorithm that computes the distance between each car (recognized images) multiple times by second
- Week 10:
- Arthur: Implement the custom UDP transmission protocol (with sequence number in the header) in the application
- Week 11:
- Arthur: Work on the custom UDP protocol with sequence number and catch up on any delay if necessary
- Week 12:
- Arthur, Albert and Daniel: Depending on time limitations, train a classification model on custom images (one for each car) or choose existing pre-trained model for the images we will place on the roof of each car

Application should be fully done by the end of week 12.

Alongside this, each week the code will be documented and posted on GitHub.

Note: If we are stuck on implementing the distance or the coordinate system for more than one week (one week is allocated for each of those tasks) - we will move back to the implementation of last year project ”Intelligent Traffic Backend” as mentioned in 1.2.1).

13

### 5.1.3 GUI

- Week 10:
- Thomas, Albert and Daniel: Designing the MiniMap and starting to work on the GUI
- Week 11:
- Thomas, Albert and Daniel: Finalizing the GUI and linking it to the server
- Week 12:
- Albert and Daniel: Designing and coding the controller iOS app
- Week 13:
- Albert and Arthur: Connecting everything to the server (+ test)

### 5.2 Hardware deadlines

### 5.2.1 Cars

- Week 7 and 8:
- Thomas and Albert: Design the car in 3D
- Week 9:
- Thomas and Albert: Printing of the car, perfection of the parts and code for the car to run (+ test)

### 5.2.2 Tracks

- Week 7:
- Hugo: Code checkpoints and power ups with blanks
- Daniel: Design + print bridge on Autodesk360
- Week 8 and 9:
- Hugo: Take code from MPC part to implement checkpoints
- Daniel: Build circuit + test tape detection
- Week 10:
- Daniel: Figure out optimal space between checkpoints + design circuit walls
- Week 11:
- Hugo: Take code from cars part to implement power ups
- Daniel: Print circuit walls + test bridge and walls
- Week 12:
- Hugo: Fix potential bugs in the code
- Week 13:
- Hugo: Try to implement new power ups and/or animations

14

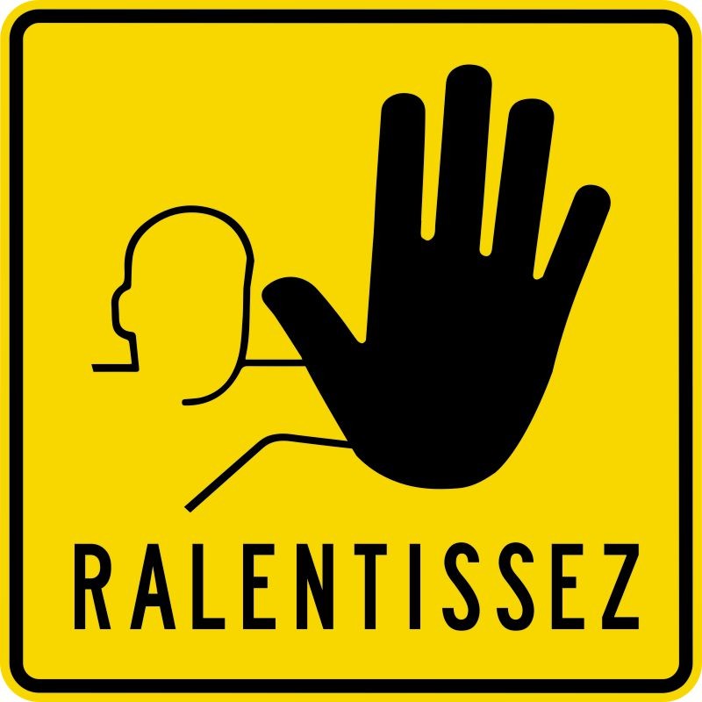
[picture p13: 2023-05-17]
Image/PowerUp/ralentir.jpg

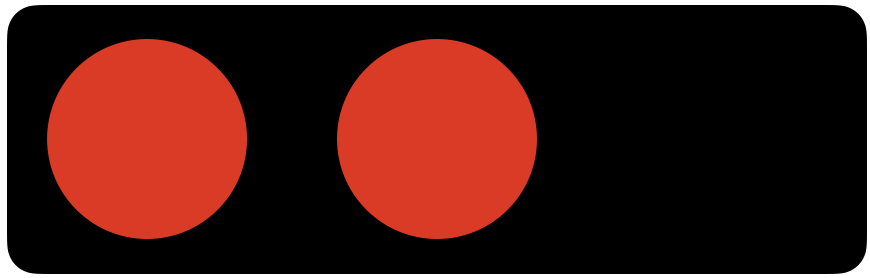
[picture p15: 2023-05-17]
Image/Feu_Depart/Feu_3.png

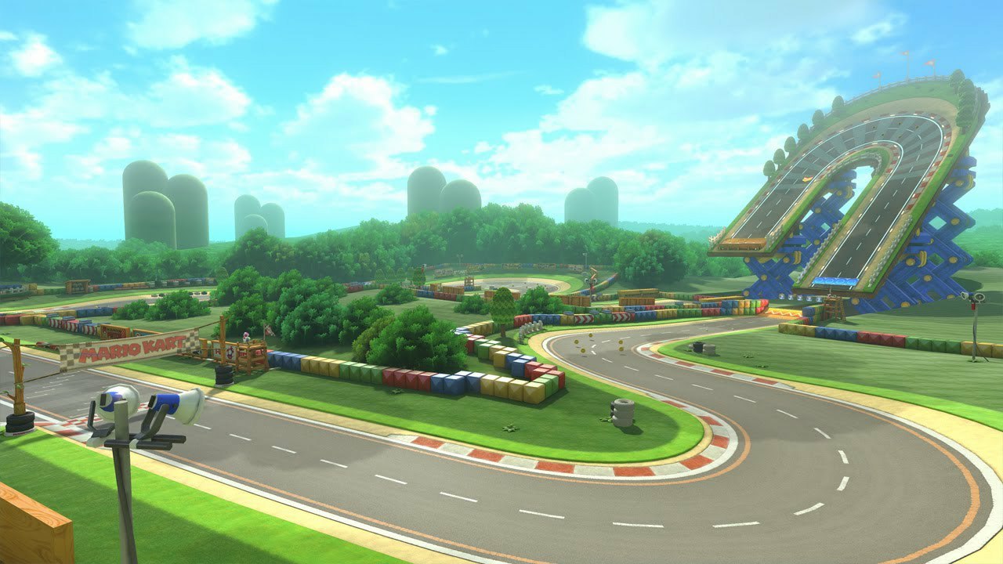
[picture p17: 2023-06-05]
Image/image_fond.jpg

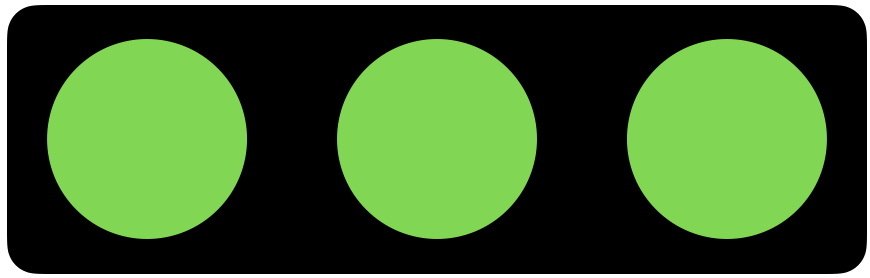
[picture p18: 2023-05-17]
Image/Feu_Depart/Feu_5.png

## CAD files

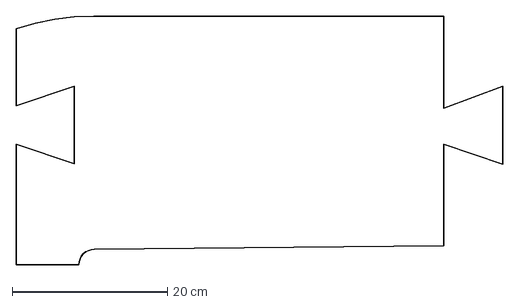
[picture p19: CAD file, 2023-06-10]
circuit/dxf parts/c22 v2.dxf
62.6 x 32.0 cm

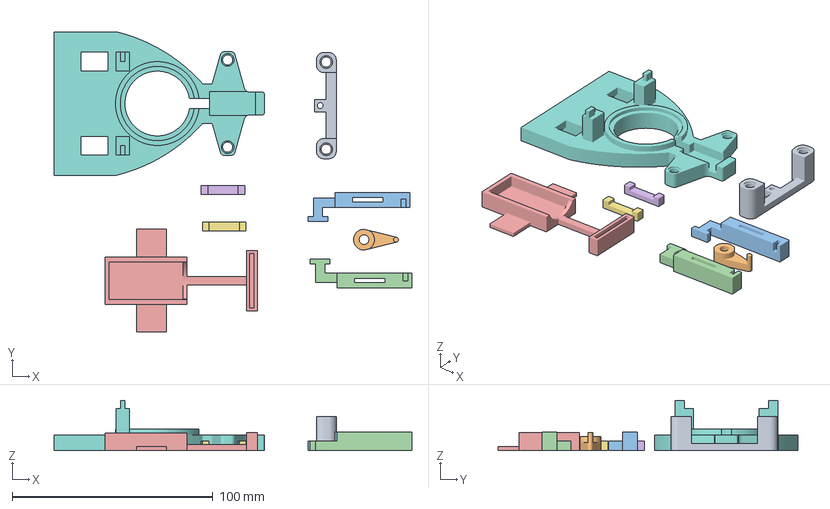
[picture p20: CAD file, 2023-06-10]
Printing Set/Set_1_S.3mf
178.3 x 149.7 x 25.0 mm
Direction.stl
Pièce Servo.stl
Structure 1.stl
Structure 2.stl
Support Moteur.stl
Pièce Structure-Moteur.stl x 2
Châssis.stl

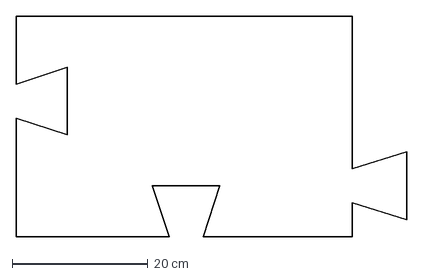
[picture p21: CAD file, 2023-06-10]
circuit/dxf parts/c322 v2.dxf
57.5 x 32.5 cm

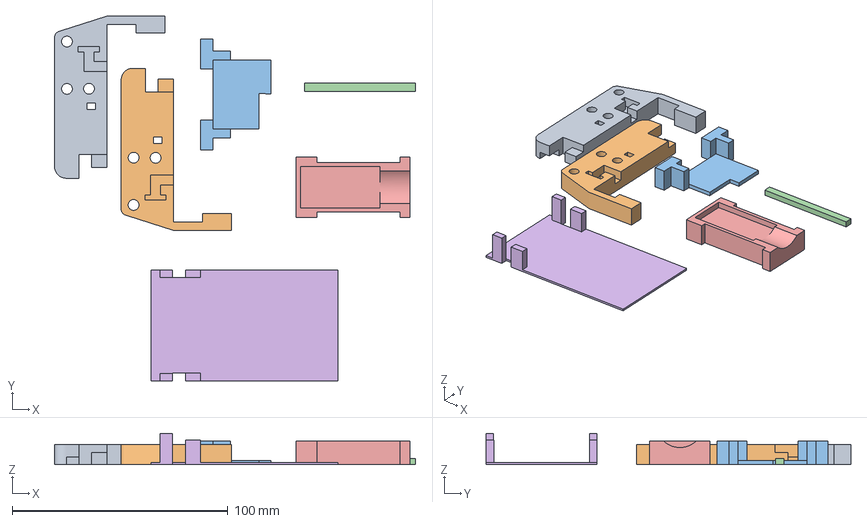
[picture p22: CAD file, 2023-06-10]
Printing Set/Set_2_S.3mf
167.2 x 168.9 x 14.5 mm
Support Differentiel 2 1.stl
Support Differentiel 2 2.stl
Support L298.stl
Bloque Moteur.stl
Support ESP-32.stl
Toit.stl

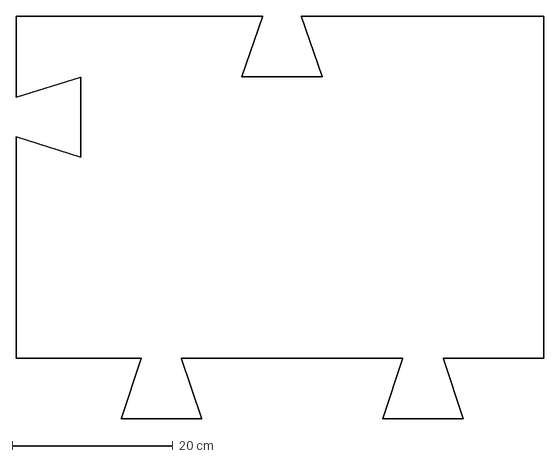
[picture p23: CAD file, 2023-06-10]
circuit/dxf parts/c311 v4.dxf
65.5 x 50.0 cm

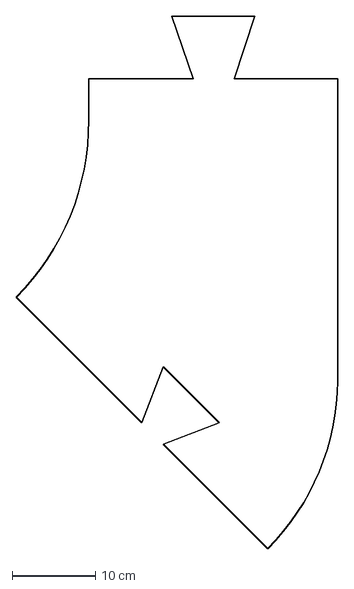
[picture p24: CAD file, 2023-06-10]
circuit/dxf parts/c25 v2.dxf
38.7 x 64.0 cm

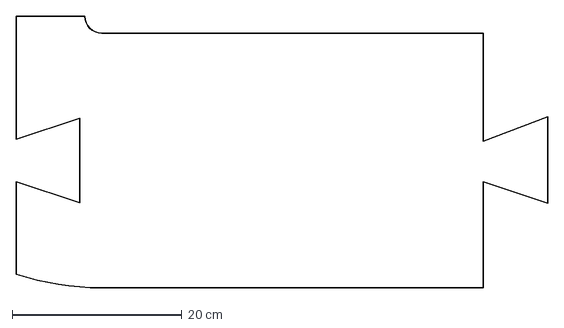
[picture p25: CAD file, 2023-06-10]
circuit/dxf parts/c21 v2.dxf
62.6 x 32.0 cm

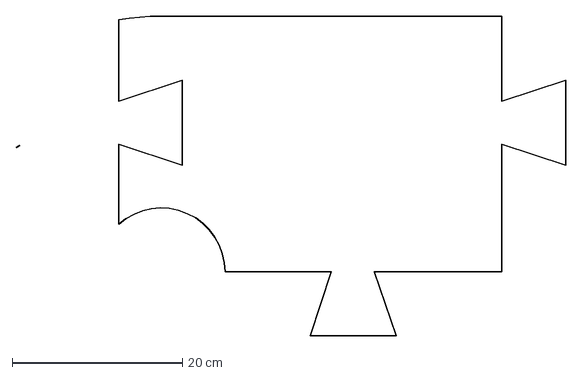
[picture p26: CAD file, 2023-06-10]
circuit/dxf parts/c332 v5.dxf
64.5 x 37.5 cm

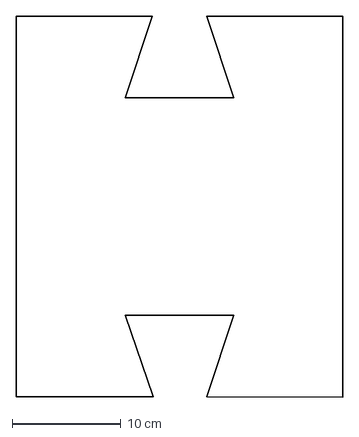
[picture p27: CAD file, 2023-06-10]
circuit/dxf parts/c27 v2.dxf
30.0 x 35.0 cm

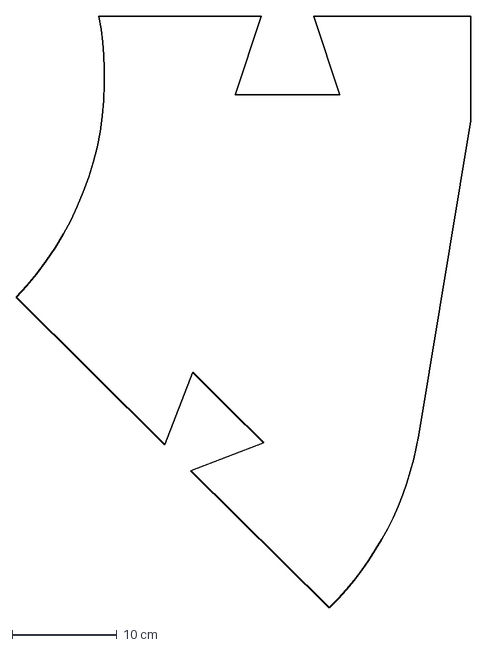
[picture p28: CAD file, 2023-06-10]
circuit/dxf parts/c26 v3.dxf
43.4 x 56.5 cm

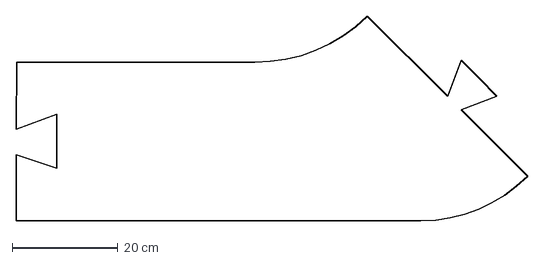
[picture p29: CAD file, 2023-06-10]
circuit/dxf parts/c24 v3.dxf
96.5 x 38.7 cm

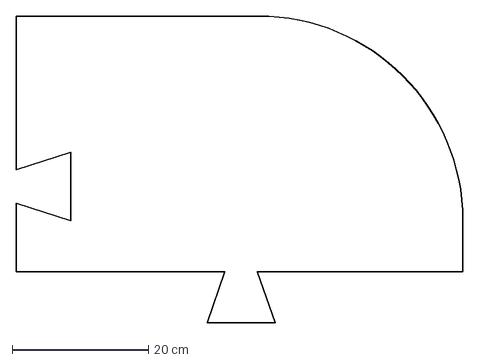
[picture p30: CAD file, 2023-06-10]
circuit/dxf parts/c312 v2.dxf
65.5 x 45.0 cm

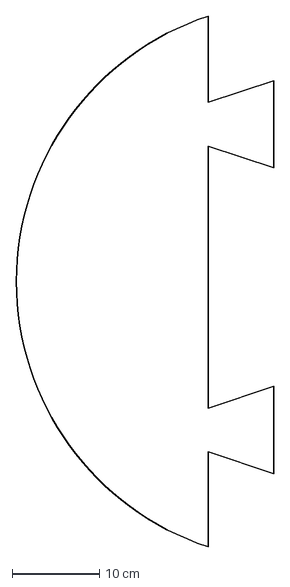
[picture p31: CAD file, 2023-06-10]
circuit/dxf parts/c1 v2.dxf
29.4 x 60.8 cm

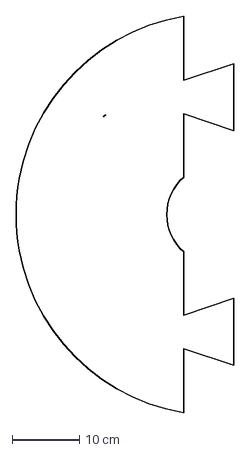
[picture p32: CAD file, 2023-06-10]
circuit/dxf parts/c4 v2.dxf
32.5 x 59.2 cm

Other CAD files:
circuit/dxf parts/c23 v2.dxf
circuit/dxf parts/c331 v2.dxf
circuit/dxf parts/c321 v4.dxf
circuit.f3d
circuit/whole circuit/circuit.f3d
phone_holder/Holder/phoneholder iphone 14promax.f3d
phone_holder/Stand/phone_stand.f3d
phone_holder/Stand/phone_stand2.f3d

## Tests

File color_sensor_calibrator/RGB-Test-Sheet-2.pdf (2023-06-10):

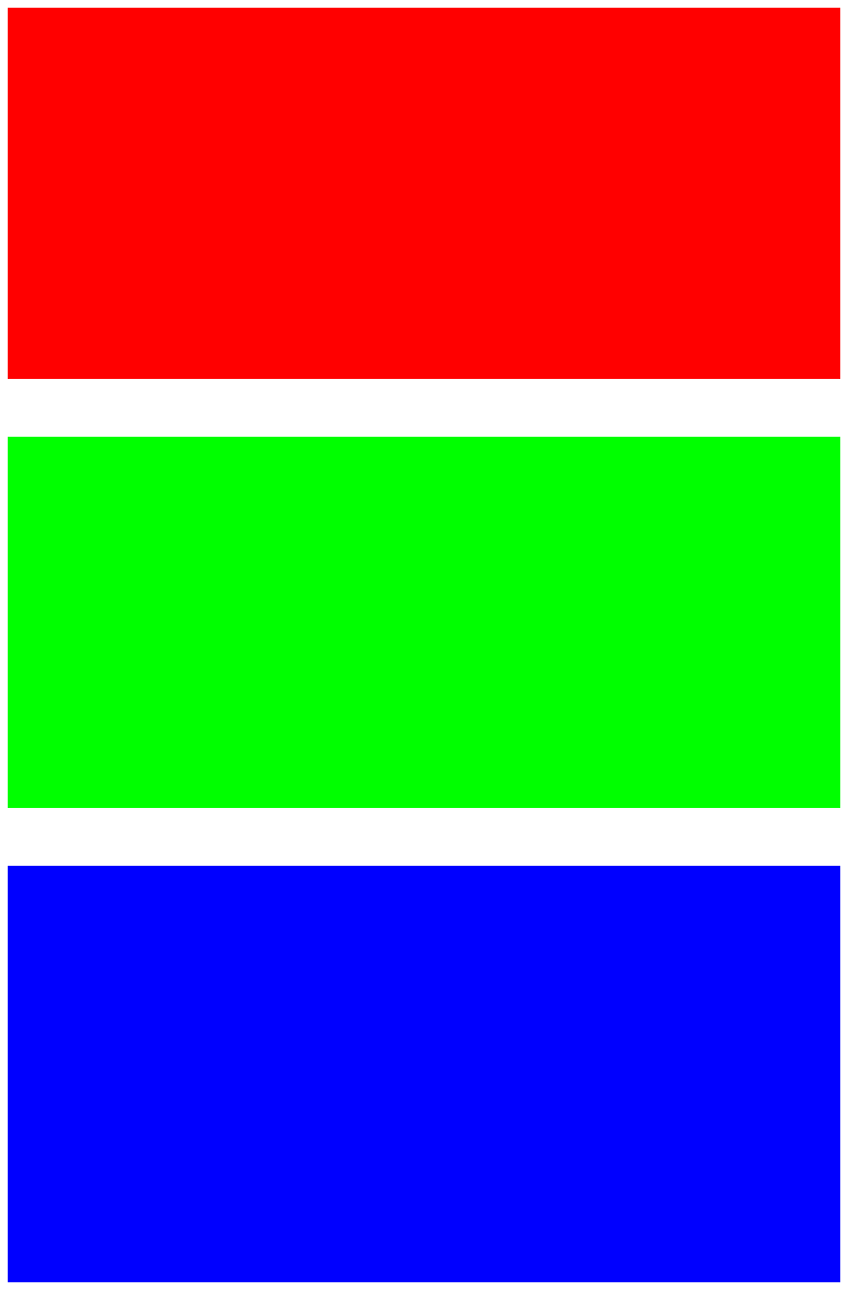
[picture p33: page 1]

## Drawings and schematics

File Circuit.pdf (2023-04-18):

Big | track | (-1 | ni

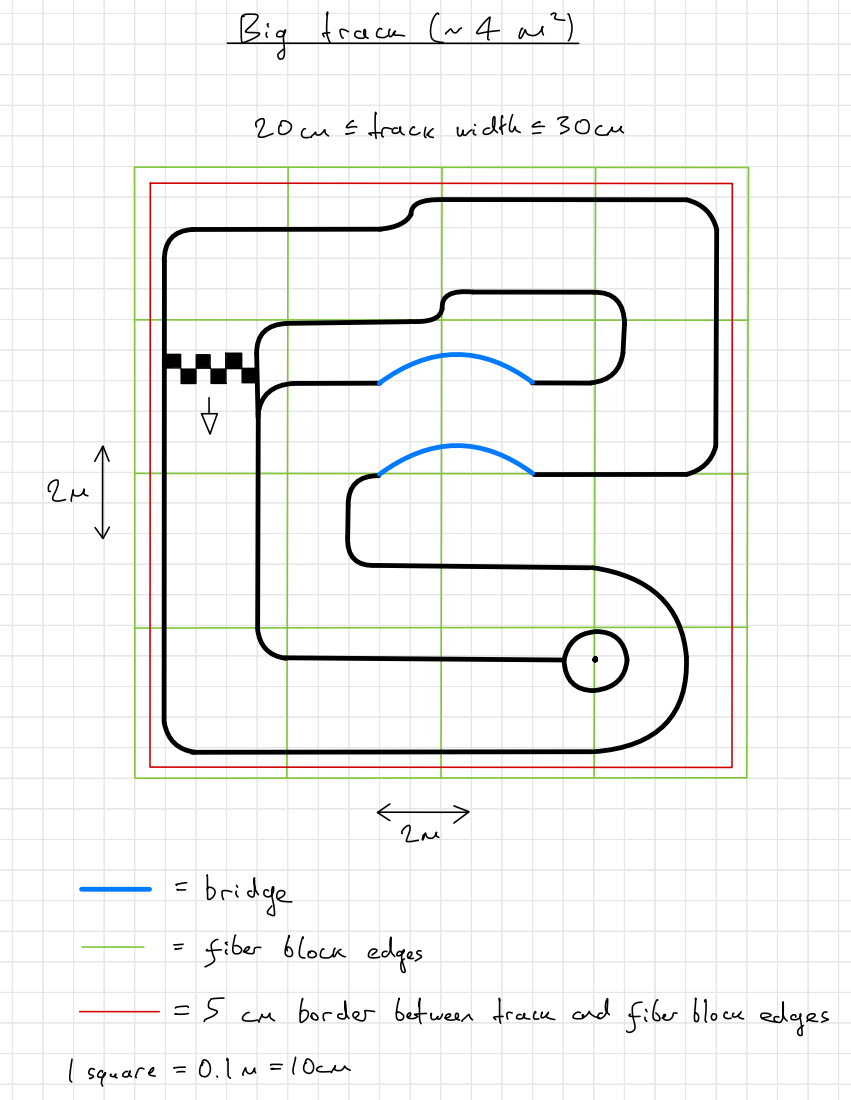
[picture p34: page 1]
20cm = trackwidth=30cm; -bridge; Fiber block; edges; border; between track; and; fiber; block; I square =

small | track | (v2m4

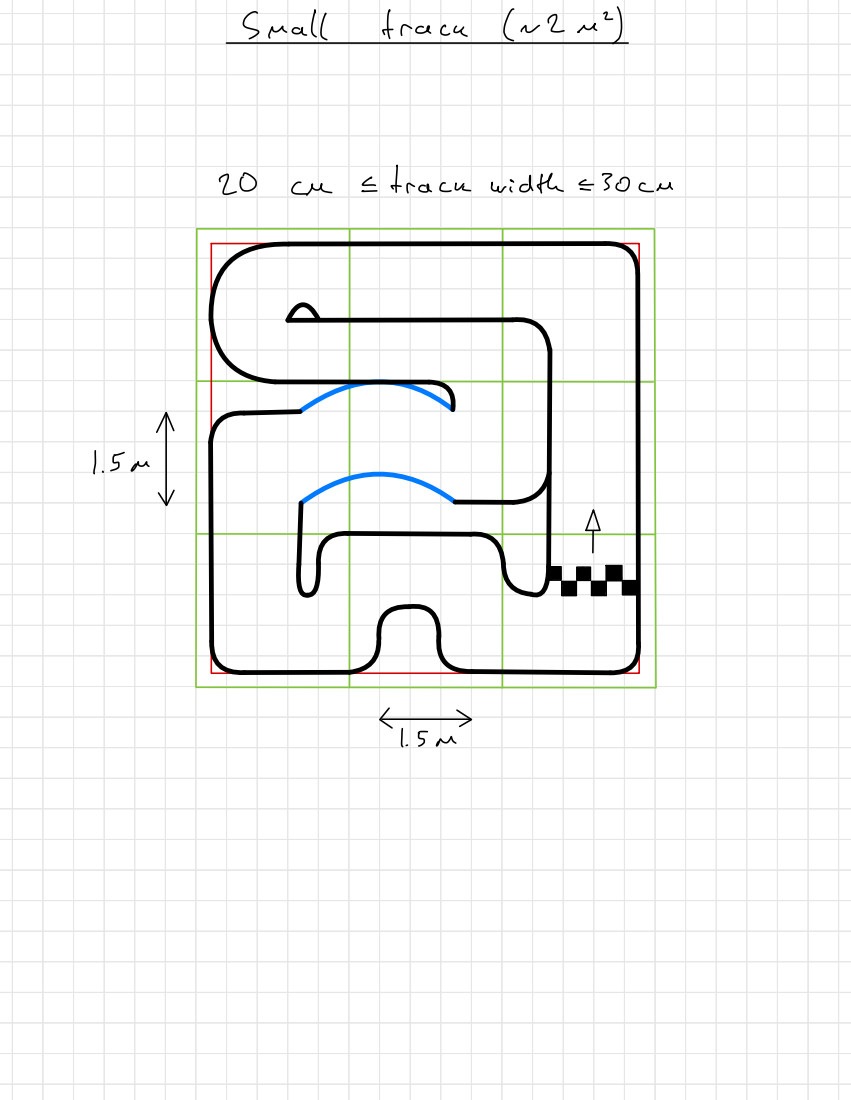
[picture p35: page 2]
track; width

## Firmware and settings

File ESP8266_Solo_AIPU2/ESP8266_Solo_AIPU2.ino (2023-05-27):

#include <ESP8266WiFi.h>
#include <Servo.h>
#include <dummy.h>
#include <math.h>
#include <ESP8266WebServer.h>
#include <cstdlib>

// Pins
#define PIN_FORWARD 12    // D6
#define PIN_REVERSE 13    // D7
#define SERVO_PIN 15      // D8

#define CAR_ID "CAR_ID_TEST"
#define CAR_ID_RESET "CAR_ID_RESET"
#define CAR_ID_PU "CAR_ID_PU"

// Assignment of the sensor pins
#define S0 4            // D2
#define S1 5            // D1
#define S2 0            // D3
#define S3 2            // D4
#define sensorOut 14    // D5

// Connection constants
const char* ssid = "albert";                    // your network SSID (name)
const char* password = "aaaabbbb";              // your network password
const char* serverAddress = "172.20.10.6";      // server address
const int serverPort = 8899;                    // server port

WiFiClient client;

// ------------------- Colour sensor code --------------------
enum Zone {
  red,
  green,
  blue,
};

Zone currZone = green;

int zoneOrPowUp = 0;
const long int PU_MAX = 5000;
long int puDelay = 0;
bool timerIsStarted = false;

bool isInMargin(int color, int theorical, int approx){
  int isIn = false;
  if (theorical - approx <= color && color <= theorical + approx){
    isIn = true;
  }
  return isIn;
}

//Calibration values (must be updated before updated before each use)
int redMin = 9174;
int redMax = 33333;
int greenMin = 9615;
int greenMax = 14705;
int blueMin = 12987;
int blueMax = 26315;
int redColor = 0;
int greenColor = 0;
int blueColor = 0;
int redFrequency = 0;
int redEdgeTime = 0;
int greenFrequency = 0;
int greenEdgeTime = 0;
int blueFrequency = 0;
int blueEdgeTime = 0;
int sensorFrequency = 0;
int sensorEdgeTime = 0;

const int RED = 2;
const int GREEN = 3;
const int BLUE = 4;
// ---------------------------------------------------------------

// Global variables
Servo myservo;
double speed_percentage = 1;
int dir = 0;
int acceleration = 1;

#define PU_NONE 0
#define PU_STOP 1
#define PU_SLOWDOWN 2
#define PU_SPEEDUP 3
// #define PU_INVERT 4

#define SLOWDOWN_PRCNT 0.86
#define SPEEDUP_PRCNT 1.15
#define NORMAL_SPEED 220
int receivedPowerup = PU_NONE;
bool isPowerupd = false;
// bool invertControls = false;

void activatePowerup() {

  srand((unsigned) time(NULL));
  // receivedPowerup = (abs(rand()) % 3) + 2;
  receivedPowerup = (abs(rand()) % 2) + 2;

  if(receivedPowerup == PU_SLOWDOWN){
    Serial.println("Slowdown");
  } else if(receivedPowerup == PU_SPEEDUP) {
    Serial.println("Speedup");
  // } else if(receivedPowerup == PU_INVERT) {
  //   Serial.println("Invert");
  } else {
    Serial.println("Error on PU");
  }

}





void setup() {

  // Pin stuff
  pinMode(PIN_FORWARD,OUTPUT);
  pinMode(PIN_REVERSE,OUTPUT);
  myservo.attach(SERVO_PIN);

  /*definition of the sensor pins*/
  pinMode(S0, OUTPUT);
  pinMode(S1, OUTPUT);
  pinMode(S2, OUTPUT);
  pinMode(S3, OUTPUT);
  pinMode(sensorOut, INPUT);

  /*Scaling the output frequency
  S0/S1
  LOW/LOW=AUS, LOW/HIGH=2%,
  HIGH/LOW=20%, HIGH/HIGH=100%*/
  digitalWrite(S0, HIGH);
  digitalWrite(S1, HIGH);

  // Start serial communication for debugging
  Serial.begin(115200);
  Serial.println();

  // Connect to Wi-Fi network
  WiFi.begin(ssid, password);
  while (WiFi.status() != WL_CONNECTED) {
    delay(1000);
    Serial.println("Connecting to WiFi...");
  }
  Serial.println("Connected to WiFi.");
  Serial.println(WiFi.localIP());

  myservo.write(90);
}



void loop() {

   // Reset powerups
  if (timerIsStarted && ((millis() - puDelay) > PU_MAX)) {
    
    timerIsStarted = false;
    puDelay = 0;
    zoneOrPowUp = currZone + 1;

    // My powerups
    receivedPowerup = PU_NONE;
    isPowerupd = false;
    // invertControls = false;
    Serial.println("Powerup reset");
  }

  //------------------------------- Colour sensor -------------------------------

  /*Determination of the photodiode type during measurement
    S2/S3
    LOW/LOW=RED, LOW/HIGH=BLUE,
    HIGH/HIGH=GREEN, HIGH/LOW=CLEAR*/
  digitalWrite(S2, LOW);
  digitalWrite(S3, LOW);
  
  /*Frequency measurement of the specified color and its as- signment to an RGB value between 0-255*/
  float(redEdgeTime) = pulseIn(sensorOut, HIGH) + pulseIn (sensorOut, LOW);
  float(redFrequency) = (1 / (redEdgeTime / 1000000)); redColor = map(redFrequency, redMax, redMin, 255, 0); 
  if (redColor > 255) {
    redColor = 255;
  }
  if (redColor < 0) {
    redColor = 0;
  }

  digitalWrite(S2, HIGH);
  digitalWrite(S3, HIGH);
  /*Frequency measurement of the specified color and its as-
  signment to an RGB value between 0-255*/
  float(greenEdgeTime) = pulseIn(sensorOut, HIGH) + pulseIn (sensorOut, LOW);
  float(greenFrequency) = (1 / (greenEdgeTime / 1000000));
  greenColor = map(greenFrequency, greenMax, greenMin, 255, 0);
  if (greenColor > 255) {
    greenColor = 255;
  }
  if (greenColor < 0) {
    greenColor = 0;
  } 
  
  digitalWrite(S2, LOW);
  digitalWrite(S3, HIGH);
  /*Frequency measurement of the specified color and its as-
  signment to an RGB value between 0-255*/
  float(blueEdgeTime) = pulseIn(sensorOut, HIGH) + pulseIn (sensorOut, LOW);
  float(blueFrequency) = (1 / (blueEdgeTime / 1000000)); blueColor = map(blueFrequency, blueMax, blueMin, 255, 0); 
  if (blueColor > 255) {
    blueColor = 255;
  }
  if (blueColor < 0) {
    blueColor = 0;
  }

  digitalWrite(S2, HIGH);
  digitalWrite(S3, LOW);


  if(isInMargin(redColor, 245, 30) && isInMargin(greenColor, 20, 30) && isInMargin(blueColor, 8, 30)) {
    // check if the sensor detects a RED tape
    if (currZone != red){
      currZone = red;
      zoneOrPowUp = RED;

    }
  } else if(isInMargin(redColor, 20, 30) && isInMargin(greenColor, 200, 30) && isInMargin(blueColor, 0, 30)) {
    // check if the sensor detects a GREEN tape
    if (currZone != green){
      currZone = green;
      zoneOrPowUp = GREEN;

    }
  } else if(isInMargin(redColor, 6, 30) && isInMargin(greenColor, 170, 30) && isInMargin(blueColor, 240, 30)) {
    // check if the sensor detects a BLUE tape
    if (currZone != blue){
      currZone = blue;
      zoneOrPowUp = BLUE;

    }
  } else if(isInMargin(redColor, 0, 30) && isInMargin(greenColor, 0, 30) && isInMargin(blueColor, 0, 30)) {
    // check if the sensor detects a black tape (POWERUP)
    if (zoneOrPowUp != 1 && !isPowerupd) {
      zoneOrPowUp = 1;            // to change back to zero when sent once
      activatePowerup();
      puDelay = millis();
      timerIsStarted = true;
    }
  } else if(isInMargin(redColor, 255, 30) && isInMargin(greenColor, 255, 30) && isInMargin(blueColor, 135, 30)) {
     // check if the sensor detects the CIRCUIT to reset powerup
    if (zoneOrPowUp != 0){ 
      zoneOrPowUp = 0;
      Serial.println("Circuit");
    }
  }

  // ----------------------------------------------------------------------------

  String data = "";

  // Connect to the server
  if (client.connect(serverAddress, serverPort)) {
    // Serial.println("Connected to server.");
    
    // Send dummy data
    client.write(CAR_ID);
    // Serial.println("Sent data to server.");

    // Wait for a response from the server
    while (client.connected()) {
      if (client.available()) {
        // Read data from the server
          data = client.readStringUntil('\n');
          // Serial.print("Received data: ");
          // Serial.println(data);
          // Close the connection

          char rcvd[data.length()+1];
          data.toCharArray(rcvd, data.length()+1);

          char* token;  // Pointer to the current token
          const char delim[] = " ";  // The delimiter (a space in this case)

          // Use strtok() to separate the string into tokens
          token = strtok(rcvd, delim);

          int count = 1;

          while (token != nullptr && count <= 2) {
              if(count == 1) {
                dir = atoi(token);
              } else if(count == 2) {
                acceleration = atoi(token);
              } else {
                break;
              }

              // Get the next token
              token = strtok(nullptr, delim);
              ++count;
          }
        
        
        // dir = 200 = stop car
        if (dir == 200) {

          printf("Stop\n");
          acceleration = 1;


        } else if(0 <= dir && dir <= 180) {

          printf("data: %s\n", data);
          printf("dir: %d\n", dir);
          myservo.write(dir);
          // acceleration = 1;

          // Car moves forward all the time unless -1 is sent

        } else {

          printf("Incorrect dir received: %d", dir);
          acceleration = 1;

        }
        client.stop();
        // Serial.println("Disconnected from server.");
      }
    }





  if(receivedPowerup == PU_STOP) {

    isPowerupd = false;
    speed_percentage = 0;
    
  } else if(isPowerupd) {

      // Should be ok]

  } else if(receivedPowerup == PU_SLOWDOWN) {

    isPowerupd = true;
    speed_percentage = SLOWDOWN_PRCNT;

  } else if(receivedPowerup == PU_SPEEDUP) {

    isPowerupd = true;
    speed_percentage = SPEEDUP_PRCNT;

  // } else if(receivedPowerup == PU_INVERT) {

  //   isPowerupd = true;
  //   invertControls = true;

  } else if(receivedPowerup == PU_NONE) {

    speed_percentage = 1;

  }
  // Controlling motors

  if(acceleration == 0) {

    analogWrite(PIN_REVERSE, NORMAL_SPEED * speed_percentage);
    digitalWrite(PIN_FORWARD, LOW);

  } else if (acceleration == 1) {

    digitalWrite(PIN_FORWARD, LOW);
    digitalWrite(PIN_REVERSE, LOW);

  } else if(acceleration == 2) {

    digitalWrite(PIN_REVERSE, LOW);
    analogWrite(PIN_FORWARD, NORMAL_SPEED * speed_percentage);

  }

  } else {

    digitalWrite(PIN_FORWARD, LOW);
    digitalWrite(PIN_REVERSE, LOW);
    Serial.println("Connection to server failed.");

  }
}

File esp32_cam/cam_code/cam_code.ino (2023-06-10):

#include "esp_camera.h"
#include <WiFi.h>
#include "esp_timer.h"
#include "img_converters.h"
#include "Arduino.h"
#include "fb_gfx.h"
#include "soc/soc.h" //disable brownout problems
#include "soc/rtc_cntl_reg.h"  //disable brownout problems
#include "esp_http_server.h"

//Replace with your network credentials
const char* ssid = "albert mac";
const char* password = "mitmitmit";

#define PART_BOUNDARY "123456789000000000000987654321"

// This project was tested with the AI Thinker Model, M5STACK PSRAM Model and M5STACK WITHOUT PSRAM
#define CAMERA_MODEL_AI_THINKER
//#define CAMERA_MODEL_M5STACK_PSRAM
//#define CAMERA_MODEL_M5STACK_WITHOUT_PSRAM

// Not tested with this model
//#define CAMERA_MODEL_WROVER_KIT

#if defined(CAMERA_MODEL_WROVER_KIT)
  #define PWDN_GPIO_NUM    -1
  #define RESET_GPIO_NUM   -1
  #define XCLK_GPIO_NUM    21
  #define SIOD_GPIO_NUM    26
  #define SIOC_GPIO_NUM    27
  
  #define Y9_GPIO_NUM      35
  #define Y8_GPIO_NUM      34
  #define Y7_GPIO_NUM      39
  #define Y6_GPIO_NUM      36
  #define Y5_GPIO_NUM      19
  #define Y4_GPIO_NUM      18
  #define Y3_GPIO_NUM       5
  #define Y2_GPIO_NUM       4
  #define VSYNC_GPIO_NUM   25
  #define HREF_GPIO_NUM    23
  #define PCLK_GPIO_NUM    22

#elif defined(CAMERA_MODEL_M5STACK_PSRAM)
  #define PWDN_GPIO_NUM     -1
  #define RESET_GPIO_NUM    15
  #define XCLK_GPIO_NUM     27
  #define SIOD_GPIO_NUM     25
  #define SIOC_GPIO_NUM     23
  
  #define Y9_GPIO_NUM       19
  #define Y8_GPIO_NUM       36
  #define Y7_GPIO_NUM       18
  #define Y6_GPIO_NUM       39
  #define Y5_GPIO_NUM        5
  #define Y4_GPIO_NUM       34
  #define Y3_GPIO_NUM       35
  #define Y2_GPIO_NUM       32
  #define VSYNC_GPIO_NUM    22
  #define HREF_GPIO_NUM     26
  #define PCLK_GPIO_NUM     21

#elif defined(CAMERA_MODEL_M5STACK_WITHOUT_PSRAM)
  #define PWDN_GPIO_NUM     -1
  #define RESET_GPIO_NUM    15
  #define XCLK_GPIO_NUM     27
  #define SIOD_GPIO_NUM     25
  #define SIOC_GPIO_NUM     23
  
  #define Y9_GPIO_NUM       19
  #define Y8_GPIO_NUM       36
  #define Y7_GPIO_NUM       18
  #define Y6_GPIO_NUM       39
  #define Y5_GPIO_NUM        5
  #define Y4_GPIO_NUM       34
  #define Y3_GPIO_NUM       35
  #define Y2_GPIO_NUM       17
  #define VSYNC_GPIO_NUM    22
  #define HREF_GPIO_NUM     26
  #define PCLK_GPIO_NUM     21

#elif defined(CAMERA_MODEL_AI_THINKER)
  #define PWDN_GPIO_NUM     32
  #define RESET_GPIO_NUM    -1
  #define XCLK_GPIO_NUM      0
  #define SIOD_GPIO_NUM     26
  #define SIOC_GPIO_NUM     27
  
  #define Y9_GPIO_NUM       35
  #define Y8_GPIO_NUM       34
  #define Y7_GPIO_NUM       39
  #define Y6_GPIO_NUM       36
  #define Y5_GPIO_NUM       21
  #define Y4_GPIO_NUM       19
  #define Y3_GPIO_NUM       18
  #define Y2_GPIO_NUM        5
  #define VSYNC_GPIO_NUM    25
  #define HREF_GPIO_NUM     23
  #define PCLK_GPIO_NUM     22
#else
  #error "Camera model not selected"
#endif

static const char* _STREAM_CONTENT_TYPE = "multipart/x-mixed-replace;boundary=" PART_BOUNDARY;
static const char* _STREAM_BOUNDARY = "\r\n--" PART_BOUNDARY "\r\n";
static const char* _STREAM_PART = "Content-Type: image/jpeg\r\nContent-Length: %u\r\n\r\n";

httpd_handle_t stream_httpd = NULL;

static esp_err_t stream_handler(httpd_req_t *req){
  camera_fb_t * fb = NULL;
  esp_err_t res = ESP_OK;
  size_t _jpg_buf_len = 0;
  uint8_t * _jpg_buf = NULL;
  char * part_buf[64];

  res = httpd_resp_set_type(req, _STREAM_CONTENT_TYPE);
  if(res != ESP_OK){
    return res;
  }

  while(true){
    fb = esp_camera_fb_get();
    if (!fb) {
      Serial.println("Camera capture failed");
      res = ESP_FAIL;
    } else {
      if(fb->width > 400){
        if(fb->format != PIXFORMAT_JPEG){
          bool jpeg_converted = frame2jpg(fb, 80, &_jpg_buf, &_jpg_buf_len);
          esp_camera_fb_return(fb);
          fb = NULL;
          if(!jpeg_converted){
            Serial.println("JPEG compression failed");
            res = ESP_FAIL;
          }
        } else {
          _jpg_buf_len = fb->len;
          _jpg_buf = fb->buf;
        }
      }
    }
    if(res == ESP_OK){
      size_t hlen = snprintf((char *)part_buf, 64, _STREAM_PART, _jpg_buf_len);
      res = httpd_resp_send_chunk(req, (const char *)part_buf, hlen);
    }
    if(res == ESP_OK){
      res = httpd_resp_send_chunk(req, (const char *)_jpg_buf, _jpg_buf_len);
    }
    if(res == ESP_OK){
      res = httpd_resp_send_chunk(req, _STREAM_BOUNDARY, strlen(_STREAM_BOUNDARY));
    }
    if(fb){
      esp_camera_fb_return(fb);
      fb = NULL;
      _jpg_buf = NULL;
    } else if(_jpg_buf){
      free(_jpg_buf);
      _jpg_buf = NULL;
    }
    if(res != ESP_OK){
      break;
    }
    //Serial.printf("MJPG: %uB\n",(uint32_t)(_jpg_buf_len));
  }
  return res;
}

void startCameraServer(){
  httpd_config_t config = HTTPD_DEFAULT_CONFIG();
  config.server_port = 80;

  httpd_uri_t index_uri = {
    .uri       = "/",
    .method    = HTTP_GET,
    .handler   = stream_handler,
    .user_ctx  = NULL
  };
  
  //Serial.printf("Starting web server on port: '%d'\n", config.server_port);
  if (httpd_start(&stream_httpd, &config) == ESP_OK) {
    httpd_register_uri_handler(stream_httpd, &index_uri);
  }
}

void setup() {
  WRITE_PERI_REG(RTC_CNTL_BROWN_OUT_REG, 0); //disable brownout detector
 
  Serial.begin(115200);
  Serial.setDebugOutput(false);
  
  camera_config_t config;
  config.ledc_channel = LEDC_CHANNEL_0;
  config.ledc_timer = LEDC_TIMER_0;
  config.pin_d0 = Y2_GPIO_NUM;
  config.pin_d1 = Y3_GPIO_NUM;
  config.pin_d2 = Y4_GPIO_NUM;
  config.pin_d3 = Y5_GPIO_NUM;
  config.pin_d4 = Y6_GPIO_NUM;
  config.pin_d5 = Y7_GPIO_NUM;
  config.pin_d6 = Y8_GPIO_NUM;
  config.pin_d7 = Y9_GPIO_NUM;
  config.pin_xclk = XCLK_GPIO_NUM;
  config.pin_pclk = PCLK_GPIO_NUM;
  config.pin_vsync = VSYNC_GPIO_NUM;
  config.pin_href = HREF_GPIO_NUM;
  config.pin_sscb_sda = SIOD_GPIO_NUM;
  config.pin_sscb_scl = SIOC_GPIO_NUM;
  config.pin_pwdn = PWDN_GPIO_NUM;
  config.pin_reset = RESET_GPIO_NUM;
  config.xclk_freq_hz = 20000000;
  config.pixel_format = PIXFORMAT_JPEG; 
  
  if(psramFound()){
    config.frame_size = FRAMESIZE_SVGA;
    config.jpeg_quality = 63;
    config.fb_count = 10;
  } else {
    config.frame_size = FRAMESIZE_SVGA;
    config.jpeg_quality = 63;
    config.fb_count = 10;
  }
  
  // Camera init
  esp_err_t err = esp_camera_init(&config);
  if (err != ESP_OK) {
    Serial.printf("Camera init failed with error 0x%x", err);
    return;
  }
  // Wi-Fi connection
  WiFi.begin(ssid, password);
  while (WiFi.status() != WL_CONNECTED) {
    delay(500);
    Serial.print(".");
  }
  Serial.println("");
  Serial.println("WiFi connected");
  
  Serial.print("Camera Stream Ready! Go to: http://");
  Serial.print(WiFi.localIP());
  
  // Start streaming web server
  startCameraServer();
}

void loop() {
  delay(50);
}

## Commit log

2023-04-18 Added Arduino test code and mouse tracker
2023-04-18 Added circuit sketch
2023-04-19 new circuit
    [circuit.f3d]
2023-04-19 2x2 circuit
    [circuit.f3d]
2023-04-21 circuit finit
    [circuit.f3d]
2023-04-22 images circuit
2023-04-24 Finished coordinate system on Arduino
2023-04-24 flow map pas fini
2023-04-24 flow map 20x20 fini
2023-04-24 flowmap image
2023-04-26 UPDATE: move flowmap to server
2023-05-02 Arduino code merged
2023-05-02 Added arduino test code
2023-05-02 Calibrated constants for Arduino car to work
2023-05-02 FIX: comment out bluetooth socket
2023-05-09 UPDATE: small changes to remove time_delta as attribute of MainServer and print attributes not arguments in Grid
2023-05-10 FlowMap pygame test
2023-05-15 NEW: Powerups
2023-05-15 Fixed send/rcv data in PowerUp control on Arduino
2023-05-16 Working powerups.
2023-05-16 Added ESP32 code
2023-05-16 UPDATE: server for powerups
2023-05-16 UPDATE: esp32code with calibration
2023-05-21 Cleaned up old code (removed mouse tracker + old unused Arduino code)
2023-05-22 UPDATE: fix grid setup from camera
2023-05-22 Added powerup only on car code
2023-05-22 Colour sensor port updated
2023-05-23 Updated Arduino AI code
2023-05-27 UPDATE: launch gui from main thread
2023-05-27 DEBUG: change print statements
2023-05-27 NEW: Arduino code working with joysticks
2023-05-27 UPDATE: change order of buttons for joystick
2023-05-27 FIX: wificlient created in loop
    [ESP8266_Solo_AIPU2.ino]
2023-05-27 arduino not finished (powup left)
2023-05-27 FIX: continuous reconnection from Arduino
    [ESP8266_Solo_AIPU2.ino]
2023-05-27 arduino fini (notmalement)
2023-05-29 arduino high
2023-05-29 UPDATE: add correct connection to HIGH
    [ESP8266_Solo_AIPU_High.ino]
2023-05-29 UPDATE: fix connection issues Arduino
    [ESP8266_Solo_AIPU_High.ino]
2023-05-29 fixup! UPDATE: fix connection issues Arduino
    [ESP8266_Solo_AIPU_High.ino]
2023-05-29 fixup! fixup! UPDATE: fix connection issues Arduino
    [ESP8266_Solo_AIPU_High.ino]
2023-05-29 UPDATE: Powerups
2023-05-29 FIX: small delay for packets in cars
    [ESP8266_Solo_AIPU_High.ino]
2023-05-29 fixup! Merge branch 'test-ai' of github.com:therokdaba/MIT---MPC-Planner into test-ai
    [ESP8266_Solo_AIPU_High.ino]
2023-05-29 new flow map
2023-06-01 Updated FlowMap
2023-06-01 Revert "Merge branch 'test-ai' of github.com:therokdaba/MIT---MPC-Planner into test-ai"
    This reverts commit 4256a38092cfc1f64595bd694f6d79fbf4b5f1ce, reversing
    changes made to ddd32a41123cc46e4dabe41e5a18fe503ced8d35.
    [ESP8266_Solo_AIPU_High.ino]
2023-06-01 out of zone fixed
    [ESP8266_Solo_AIPU_High.ino]
2023-06-01 gui flowmap 40
2023-06-01 UPDATE: flowmap calibration
2023-06-02 NEW: Powerups and zones server side
2023-06-02 drapeap de fin
2023-06-02 fond circuit
2023-06-02 GUI powerups
2023-06-05 flowmap changes
2023-06-06 UPDATE: comment out circuit_2 and fix import
2023-06-07 STYLE: comment out when we are not using the color sensors
2023-06-08 image circuit_2
2023-06-10 NEW: add code for cars
    [Set_1_S.3mf, Set_2_S.3mf, c1 v2.dxf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]
